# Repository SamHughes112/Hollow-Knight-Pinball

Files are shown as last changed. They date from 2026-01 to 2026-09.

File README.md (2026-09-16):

# Hollow-Knight-Pinball
Hollow Knight Pinball - Custom Pinball Machine

For stardance (if your not here for stardance just ignore this) I am submitting my playfield CAD which is in "CAD Files"

Playfield_v2 copy
playfield_v2_shooter_lane copy
playfield_v2_angled copy

Screenshot 2026-06-24 at 7 18 13 AM

The Demo Link is: https://cad.onshape.com/documents/46a9741959470dc46e7c739c/w/06598aae82bc74cde6aa571a/e/faa4b0390295b76dec385a50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

Quickstart:
The onshape link should work right out of the box if you just want to look. 

If you are looking to produce your own playfield you can either download it from the onshape link or use the .step in the repository under "CAD Files" it is named "Hollow_Knight_Pinball_Playfield.step" you will need access to a CNC machine obviously to produce it (use 1/2 inch plywood 9+ plies ideally make sure it is very flat). In terms of settings you want a small ish bit the smallest hole on the playfield is 0.125 inches or 1/8th so it has to be smaller than that however some of the other parts have fine details so you might want to use something even smaller at least for those although it would probably work with a 1/8th bit. Keep the depth of your cut under half your bit diameter and run at 16-18000 RPMs. I highly recommend doing some tests before trying to cut the whole large piece.

Features
- Holes for posts and ball guide for playfield geometry (the path of the ball)
- Holes for mechs such as pop bumpers, slingshots, ball troughs, targets, etc
- Curved cuts for the shooter lane exit to have a smooth transition onto the playfield and to have better contact from the plunger and keep the ball going straight
- Holes for general illumination lighting
- Holes for inserts (clear pieces of plastic that are lit underneath) with a ledge at the correct height for easier setting

How it works
Most of the sketches are drawn on a plane that is set to be at the top of the playfield, I then use an extrude remove to remove as much material down as I need to (typically all the way through the playfield). For complicated shapes I made templates which could be helpful if you wanted to make your own machine (that isn't the same layout as mine). Here are some photos of the templates for the inserts and for the 1 inch circular target cutout.

Screenshot 2026-06-09 at 10 05 55 PM
Screenshot 2026-06-21 at 9 42 10 AM

Other than that there was obviously a lot of measuring to convert my physical first draft into the CAD so that it could be machined and much neater. The only other thing I want to talk about is the indent in the shooter lane because I think it's kind of cool and was quite a challenge. 

Screenshot 2026-06-24 at 7 55 51 AM

^ is what I am talking about. First off I'm sure there are better ways to do this but what other people ultimately helped me figure out is that I could draw a v shape on a plane tilted just a couple of degrees and then I could do a remove extrude out of both sides of that to get the general shape. Then I just used some other tools to round the edges to help it function better but more importantly to reduce damage over time from the ball.

Credits
My friends and also the custom pinball community were both incredibly helpful and I can't even count the number of stupid questions they answered for me about how to do the most basic things.

AI Disclaimer: I used AI to help me figure out what tools to use since I'm new to CAD and too help with a little bit of math to figure out the radius of the rounded corners. AI did not do any of the modeling.

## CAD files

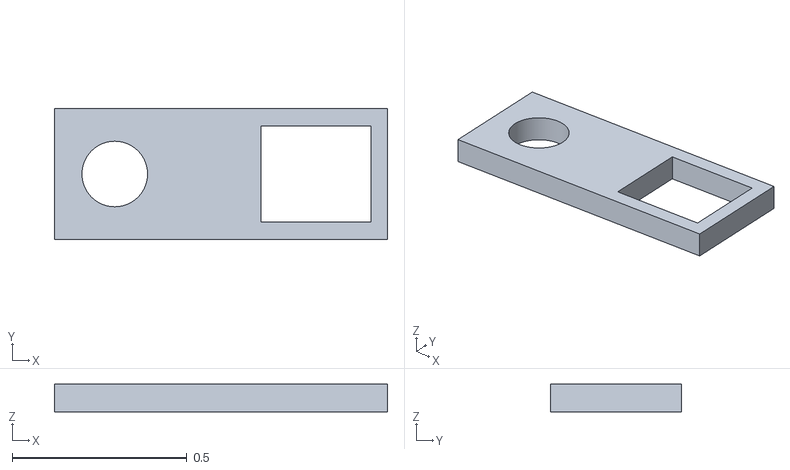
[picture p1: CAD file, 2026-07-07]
CAD Files/GI:RGBW Bracket.stl
0.953 x 0.375 x 0.0787

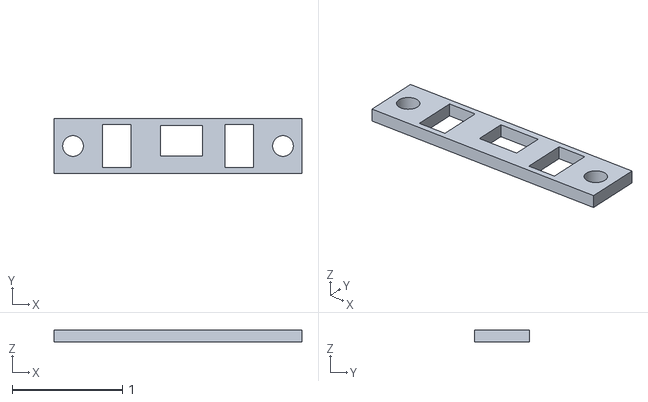
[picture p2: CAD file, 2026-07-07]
CAD Files/Branch Bracket v2.stl
2.25 x 0.5 x 0.11

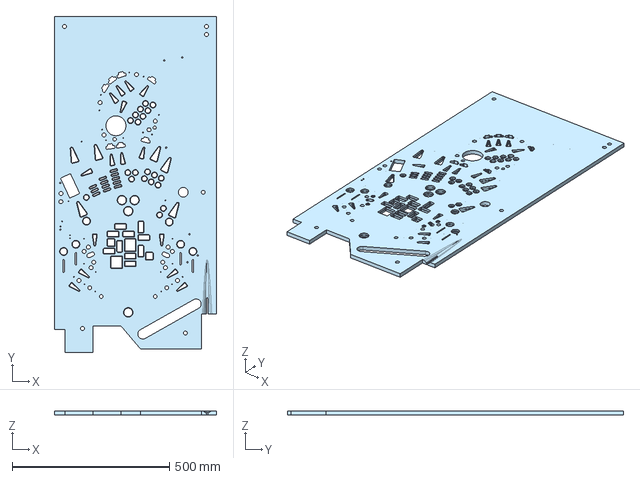
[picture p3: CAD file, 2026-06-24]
CAD Files/Hollow_Knight_Pinball_Playfield.step
514.4 x 1066.8 x 12.7 mm

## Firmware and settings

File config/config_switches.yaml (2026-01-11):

#config_version=6

switches:
  s_left_flipper:
    number: 0-0-1 #temp
    tags: left_flipper
  s_right_flipper:
    number: 0-0-2 #temp
    tags: right_flipper

#Trough switches will have to be reworked
  s_trough_1:
    number: 0-0-3 #temp
  s_trough_2:
    number: 0-0-8 #temp
  s_trough_3:
    number: 0-0-9 #temp
  s_plunger_lane:
   number: 0-0-10 #temp

#Other playfield switches will need more info once I am building them out

  s_right_outlane:
    number: 0-0-11 #temp
  s_right_inlane:
    number: 0-0-27 #temp
  s_left_inlane:
    number: 0-0-26 #temp
  s_left_outlane:
    number: 0-0-25 #temp
  
  s_top_left_slingshot:
    number: 0-0-24 #temp
  s_bottom_left_slingshot:
    number: 0-0-19 #temp
  s_top_right_slingshot:
    number: 0-0-18 #temp
  s_bottom_right_slingshot:
    number: 0-0-17 #temp
  
  s_vuk:
    number: 0-0-16 #temp
  s_ramp:
    number: 1-0-1 #temp
  s_left_orbit:
    number: 1-0-2 #temp
  s_lane_to_pop:
    number: 1-0-3 #temp
  s_right_orbit:
    number: 1-0-8 #temp
  s_saucer:
    number: 1-0-9 #temp

  s_front_left_target:
    number: 1-0-10 #temp
  s_front_middle_target:
    number: 1-0-11 #temp
  s_front_right_target:
    number: 1-0-31 #temp
  
  s_pop_bumper:
    number: 1-0-30 #temp
  
  s_back_left_target:
    number: 1-0-29 #temp
  s_back_middle_left_target:
    number: 1-0-28 #temp
  s_back_middle_right_target:
    number: 1-0-27 #temp
  s_back_right_target:
    number: 1-0-26 #temp

  s_start:
    number: 1-0-25 #temp
    tags: start
  

  

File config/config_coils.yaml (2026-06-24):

#config_version=6

coils:
  c_flipper_left_main:
    number: 1-0-1 #temp update when assign real coil numbers
    default_pulse_ms: 
  c_flipper_left_hold:
    number: 1-0-2 #temp update when assign real coil numbers
    allow_enable: true
  c_flipper_right_main:
    number: 1-0-3 #temp update when assign real coil numbers
    default_pulse_ms:
  c_flipper_right_hold:
    number: 1-0-4 #temp update when assign real coil numbers
    allow_enable: true
  c_trough_eject:
    number: 1-0-5 #temp update when assign real coil numbers
    default_pulse_ms:

  #will need to be modified

  c_vuk_eject:
    number: 1-0-6 #temp
    default_pulse_ms:
  c_pop_bumper:
    number: 1-0-7 #temp
    default_pulse_ms:
  c_saucer_eject:
    number: 1-0-0 #temp
    default_pulse_ms:

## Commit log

2025-11-08 Adding Godot and GMC
    [plugin.cfg]
2025-11-22 Audio configurations for gmc
    [gmc.cfg]
2025-11-22 Logs and updating to 0.1.6 for gmc
    [plugin.cfg]
2025-11-22 Logs and fixing comments in gmc.cfg
    [gmc.cfg]
2025-11-23 Config file now has trough switches, coils, and plunger
2025-11-23 Attract carosel configured
    [gmc.cfg]
2025-11-23 Fixed flipper switches added more slides to attract mode
    [gmc.cfg]
2025-11-24 Added many more switches for the playfield and for the coils
2025-11-24 Configured switches to keyboard
    [gmc.cfg]
2025-11-24 Fixed an error with a target and the pop bumper and also more logs
    [gmc.cfg]
2025-11-25 Attempted to get scoring functioning but issue with ball eject mode to count right orbits implemented
    [gmc.cfg]
2025-11-25 Scoring now works for the right orbit
    [gmc.cfg]
2025-11-25 Now can fully simulate a game
    [machine_vars.yaml]
2025-11-25 Fixed scoring bugs in several files
    [machine_vars.yaml]
2025-11-25 Logs, bugfixes, and tweeks
    [machine_vars.yaml]
2025-11-25 Fixed bug with slingshots
    [gmc.cfg]
2025-11-26 Added player variables and logic for whether or not various modes are active
    [false_knight_controller.yaml]
2025-11-26 finally got player variables to not crash
    [false_knight_controller.yaml]
2025-11-26 Added frogotten crossroads
    [false_knight_controller.yaml]
2025-11-29 Made a mode active player variable
    [false_knight_controller.yaml]
2025-11-29 Still not working but end of mode code fixed
    [false_knight_controller.yaml]
2025-11-29 Carousel works and music now runs for false knight
    [false_knight_controller.yaml]
2025-11-29 Framework for soul and masks
    [mask_controller.yaml]
2025-11-30 Added vs code counter to gitignore and added assets for masks
    [mask_controller.yaml]
2026-06-24 CAD File Upload
    [Hollow_Knight_Pinball_Playfield.step, plugin.cfg]
2026-06-24 Last read me update for the CAD
